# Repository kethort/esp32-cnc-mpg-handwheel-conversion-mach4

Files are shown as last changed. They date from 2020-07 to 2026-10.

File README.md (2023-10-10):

# Mach4 Wireless (Wifi) MPG Handwheel Using ESP32 and Modbus TCP library

<p align="center">
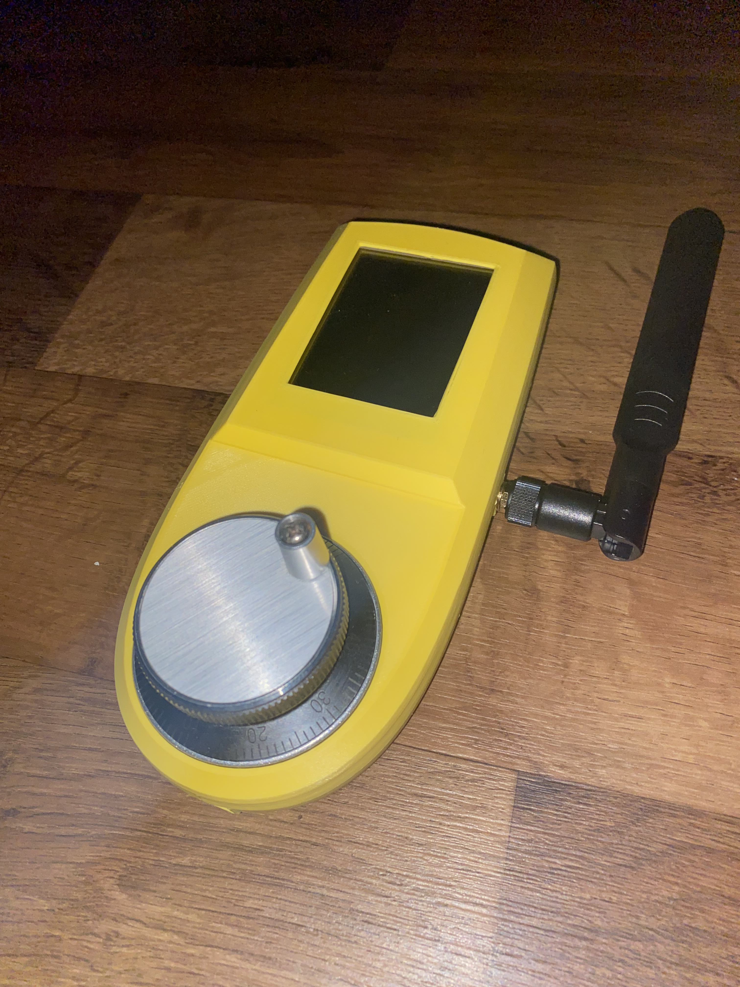
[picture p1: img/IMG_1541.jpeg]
  
</p>

<p align="center">
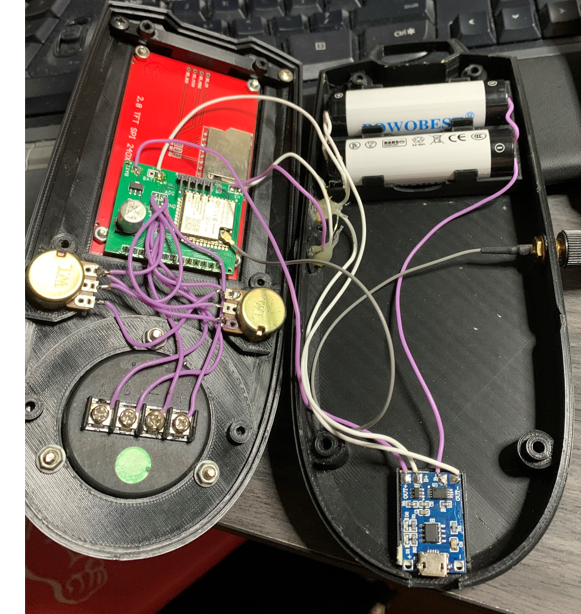
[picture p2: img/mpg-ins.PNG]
  
</p>

## Demonstration & Assembly
https://www.youtube.com/watch?v=sGhttK0reT0&t=2s <br>
https://www.youtube.com/watch?v=5fpQ3xS1Tu8&t=2s

## ESP32 Firmware and Network Setup
1. Download NodeMCU-PyFlasher.exe program from here: https://github.com/marcelstoer/nodemcu-pyflasher/releases/tag/v5.0.0
2. Connect a USB to FTDI or CP2102 to FTL programmer to the ESP32 PCB at the programmer port. 
3. Select the COM port of the programmer in the NodeMCU program.
4. Select the Mach4MPGModbus-ILI9341-Display.ino.bin file from the fw-build folder and press the Flash NodeMCU button to flash the firmware to the ESP32.
5. Reboot the ESP32.

<p align="center">
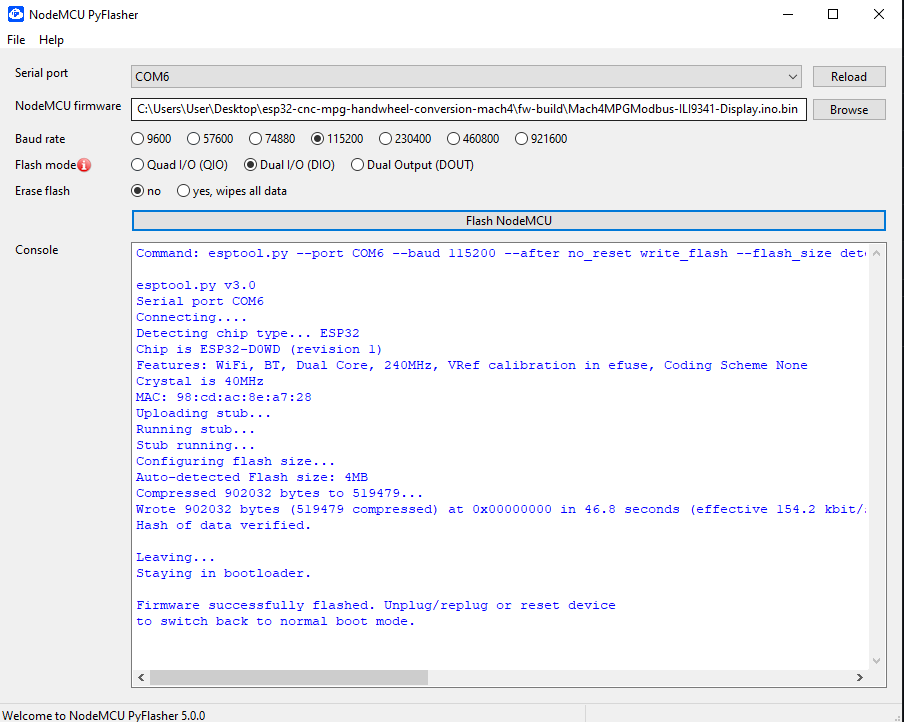
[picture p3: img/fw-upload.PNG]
  
</p>

6. The ESP32 device should show up in the list of network access points. 

<p align="center">
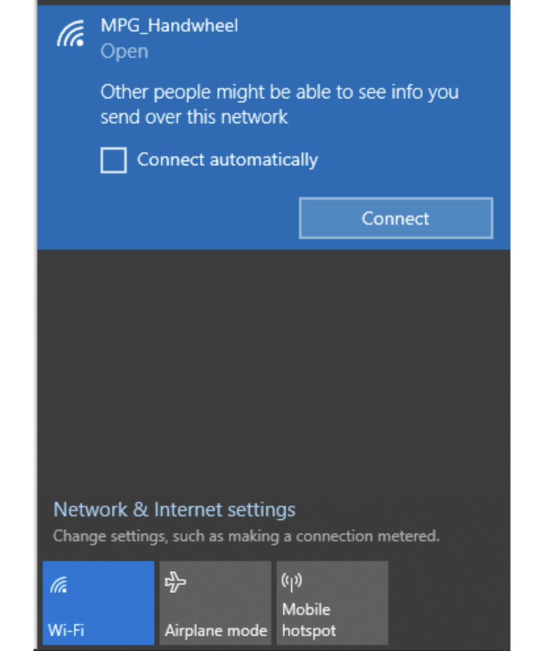
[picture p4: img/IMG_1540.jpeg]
  
</p>

7. Connect to this access point and navigate to 192.168.4.1 in a browser. 
8. Press the "Configure Wifi" button.

<p align="center">
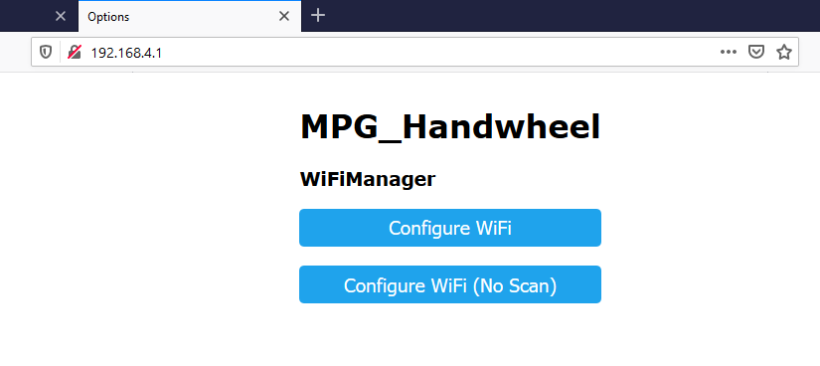
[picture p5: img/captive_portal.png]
  
</p>

9. Find your network access point and connect to it by providing your network credentials.

<p align="center">
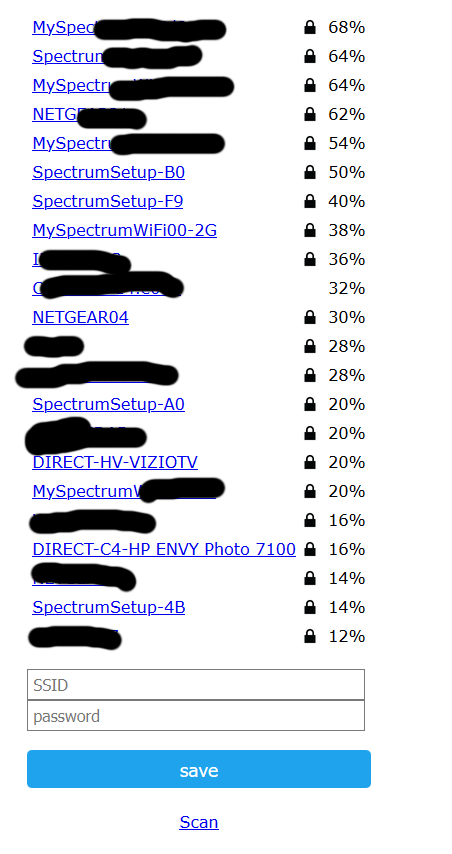
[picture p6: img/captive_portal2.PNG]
  
</p>

## Mach4 Software Setup
1. Find the local IP address of the ESP32 (espressif). 

<p align="center">
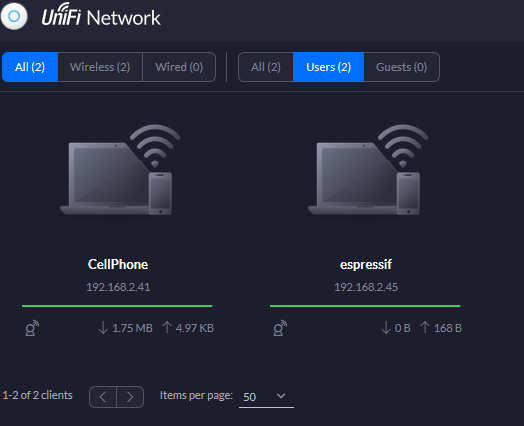
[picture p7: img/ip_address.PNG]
  
</p>

2. Launch the MPGInstaller.exe from the dist folder of the repo.
3. Select the Mach4 profile you want to update, enter the IP address of the ESP32 and press install. (if the ESP32 device is already connected to the network, and in the ARP table, the IP address should auto-populate)

<p align="center">
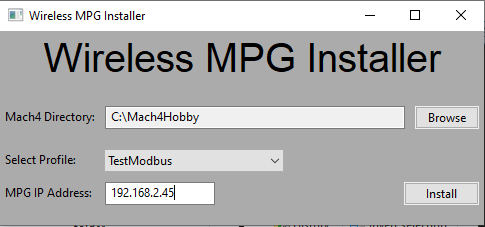
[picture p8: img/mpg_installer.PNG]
  
</p>

4. Turn on the ESP32 MPG, open Mach4 and navigate to Diagnostic->Modbus in the File Menu.
5. To connect or reconnect to the modbus device, press the stop button in the diagnostic window and then the play button. <i>(Alternatively use the Wizard instead [step 6])</i>

<p align="center">
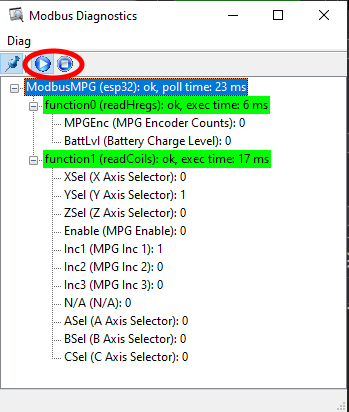
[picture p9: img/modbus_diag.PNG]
  
</p>

6. The wizard can be accessed by opening the Wizard launcher in the Mach4 file menu. (Wizard->Select Wizard->MPGWiz)
   
<p align="center">
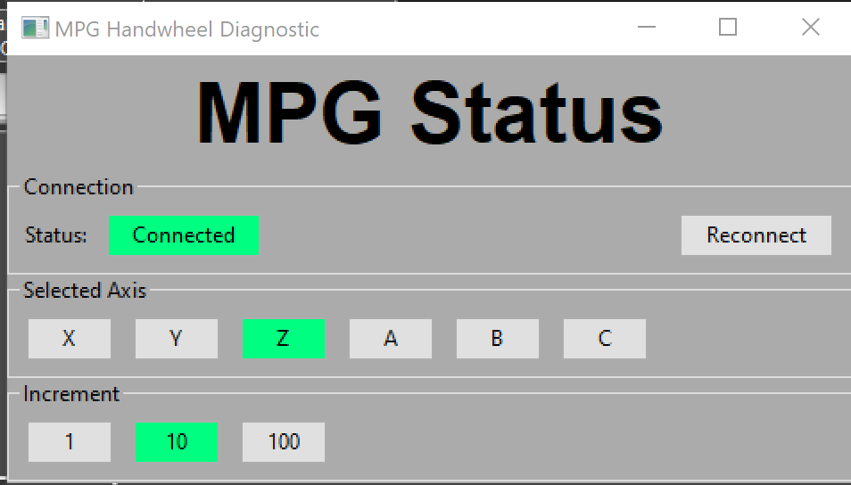
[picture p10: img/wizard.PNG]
  
</p>   

## Installer Build from Source
If you want to make changes to MPGInstaller.py and rebuild exe file:

1. Install Python
2. In elevated command line window from root directory of repo: ```pip install -r requirements.txt```
4. In command line window from root directory of repo: ```python setup.py py2exe```

The updated .exe file will be created in the dist/ folder. 

## PCB Gerber File & 3d print files for Display included
Original 3d print: https://www.thingiverse.com/thing:4539827

<p align="center">
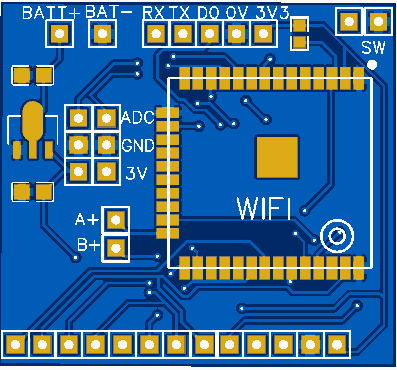
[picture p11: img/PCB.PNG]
  
</p>

<p align="center">
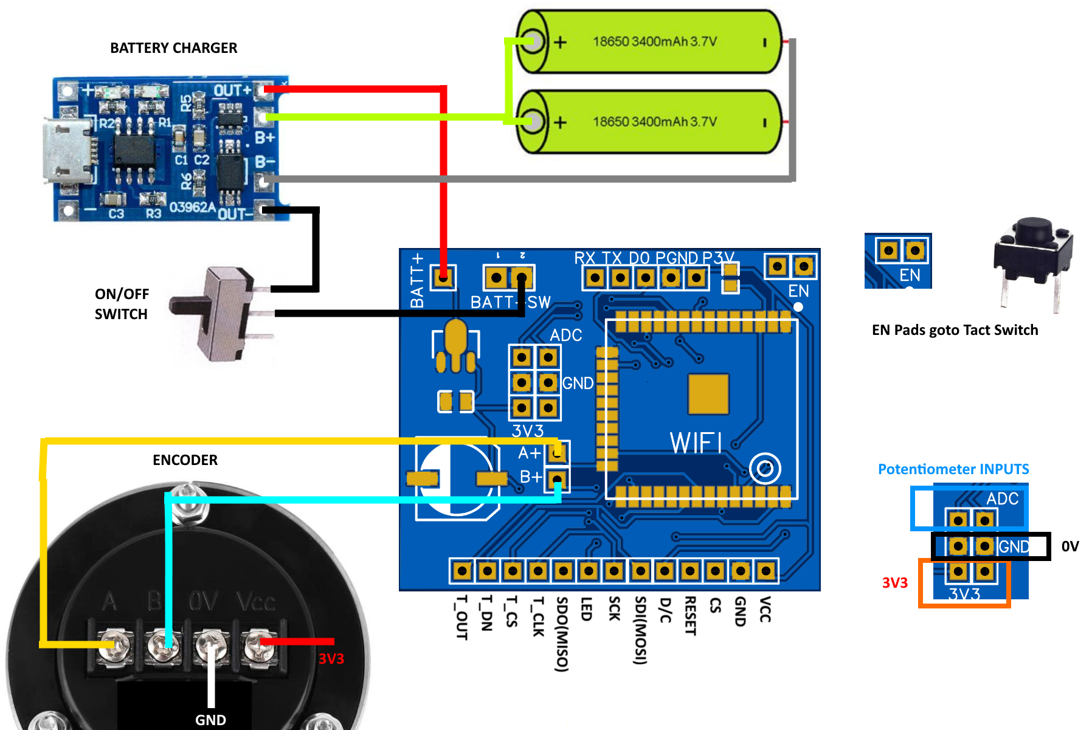
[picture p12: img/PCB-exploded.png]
  
</p>

<p align="center">
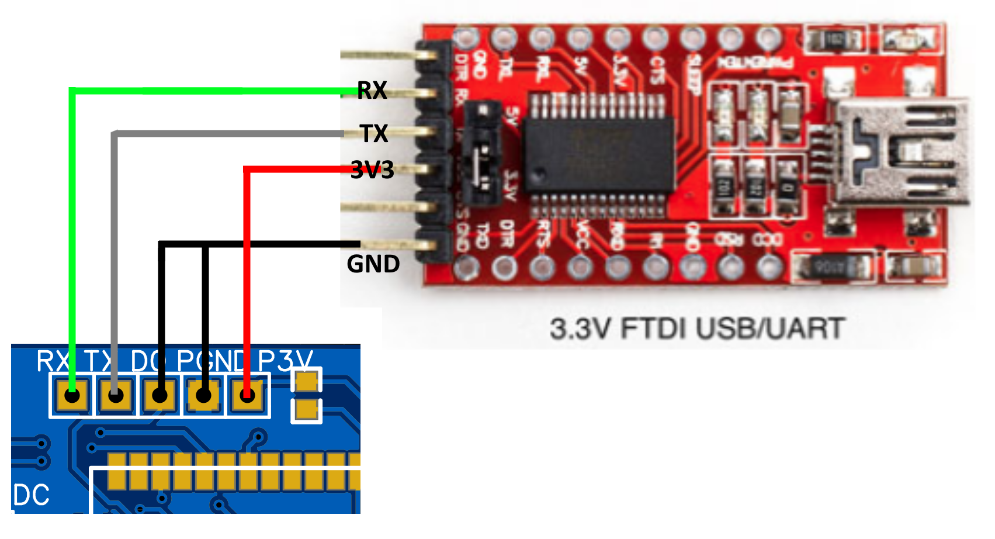
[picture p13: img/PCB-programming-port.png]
  
</p>

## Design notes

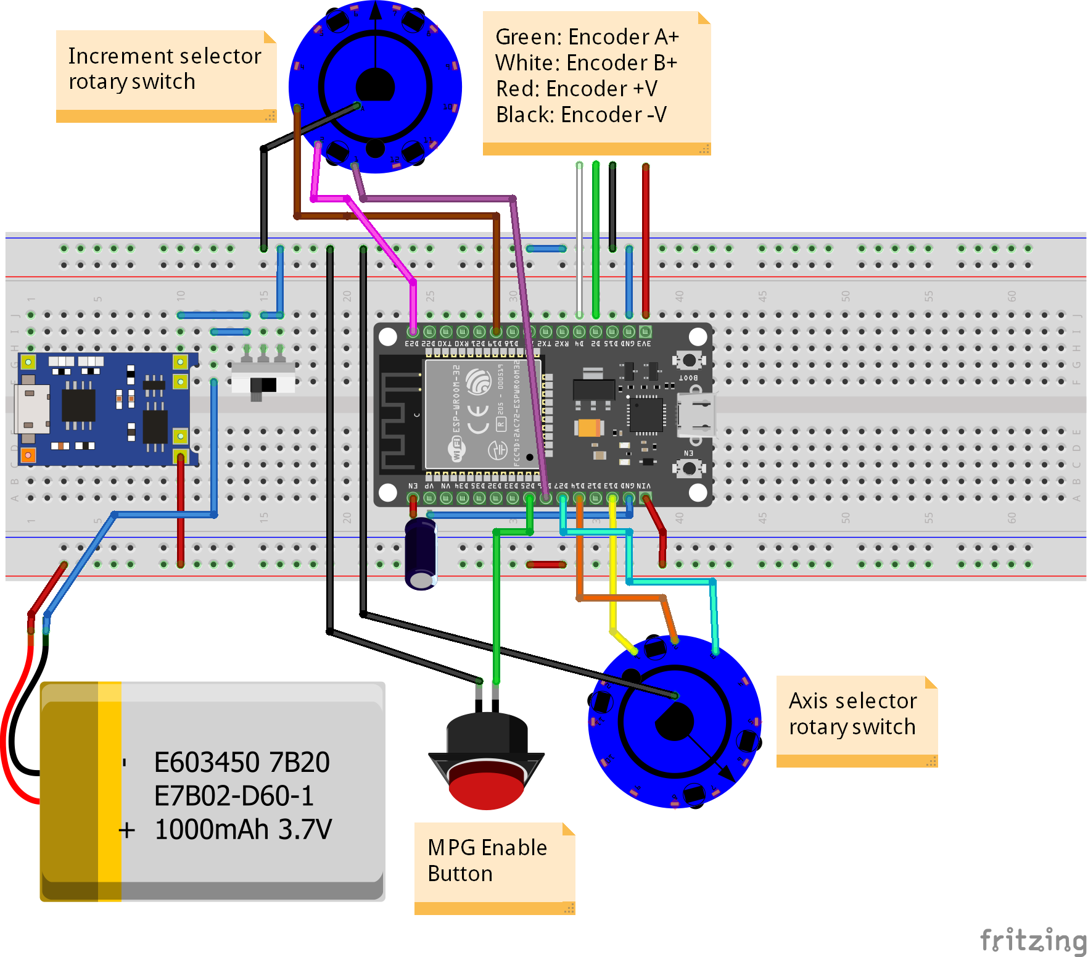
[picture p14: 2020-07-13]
img/WirelessMPG_bb.png

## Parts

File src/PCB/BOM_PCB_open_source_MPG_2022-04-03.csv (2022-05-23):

ID | Name | Designator | Footprint | Quantity | Manufacturer Part | Manufacturer | Supplier | Supplier Part | Price
1 | 1uF | C2 | C0805 | 1 | EMK212B7105KG-T | TAIYO YUDEN | LCSC | C87154 | 0.022
2 | 2.2uF | C4 | C0805 | 1 | CL21A225KOFNNNE | SAMSUNG | LCSC | C1731 | 0.022
3 | BATT- | BAT- | HDR-M-2.54_1X1 | 1 |  |  | LCSC | C81276 | 0.007
4 | BATT+ | BATT+ | HDR-M-2.54_1X1 | 1 |  |  | LCSC | C81276 | 0.007
5 | SWTCH | SWTCH | HDR-M-2.54_1X1 | 1 |  |  | LCSC | C81276 | 0.007
6 | 3V3 | 3V3,3V,J26,J10 | HDR-M-2.54_1X1 | 4 |  |  | LCSC | C81276 | 0.007
7 | D0 | D0 | HDR-M-2.54_1X1 | 1 |  |  | LCSC | C81276 | 0.007
8 | RX | RX | HDR-M-2.54_1X1 | 1 |  |  | LCSC | C81276 | 0.007
9 | TX | TX | HDR-M-2.54_1X1 | 1 |  |  | LCSC | C81276 | 0.007
10 | D25 | ADC | HDR-M-2.54_1X1 | 1 |  |  | LCSC | C81276 | 0.007
11 | D32 | SW | HDR-M-2.54_1X1 | 1 |  |  | LCSC | C81276 | 0.007
12 | GND | 0V,GND,J24,J9 | HDR-M-2.54_1X1 | 4 |  |  | LCSC | C81276 | 0.007
13 | D2 | A+ | HDR-M-2.54_1X1 | 1 |  |  | LCSC | C81276 | 0.007
14 | D4 | B+ | HDR-M-2.54_1X1 | 1 |  |  | LCSC | C81276 | 0.007
15 | HT7833 | U2 | SOT-89_L4.5-W2.5-P1.50-LS4.2-BR | 1 | HT7833 | HOLTEK | LCSC | C50936 | 0.564
16 | ESP32-WROOM-32U | U1 | WIFIM-SMD_38P-L19.2-W18.0-P1.27 | 1 | ESP32-WROOM-32U | Espressif Systems | LCSC | C328062 | 3.244
17 | D27 | J14 | HDR-M-2.54_1X1 | 1 |  |  | LCSC | C81276 | 0.007
18 | D26 | J23 | HDR-M-2.54_1X1 | 1 |  |  | LCSC | C81276 | 0.007
19 | 10K | R1 | R0603 | 1 | SDNT1608X103F3450FTF | Sunlord | LCSC | C95953 | 0.024
20 | D23 | J13,J5 | HDR-M-2.54_1X1 | 2 |  |  | LCSC | C81276 | 0.007
21 | EN | J2 | HDR-M-2.54_1X1 | 1 |  |  | LCSC | C81276 | 0.007
22 | D13 | J3 | HDR-M-2.54_1X1 | 1 |  |  | LCSC | C81276 | 0.007
23 | D15 | J4 | HDR-M-2.54_1X1 | 1 |  |  | LCSC | C81276 | 0.007
24 | D21 | J6 | HDR-M-2.54_1X1 | 1 |  |  | LCSC | C81276 | 0.007
25 | D19 | J7 | HDR-M-2.54_1X1 | 1 |  |  | LCSC | C81276 | 0.007
26 | D18 | J8,J12 | HDR-M-2.54_1X1 | 2 |  |  | LCSC | C81276 | 0.007
27 | NC | J11 | HDR-M-2.54_1X1 | 1 |  |  | LCSC | C81276 | 0.007

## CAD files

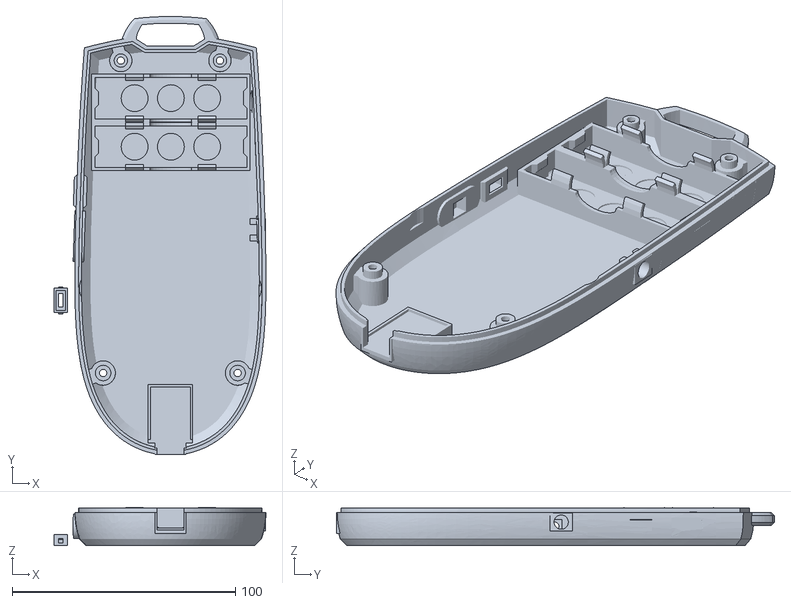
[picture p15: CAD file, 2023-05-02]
src/3d Print Files/mpg-bottom.stl
95.0 x 196.2 x 17.2

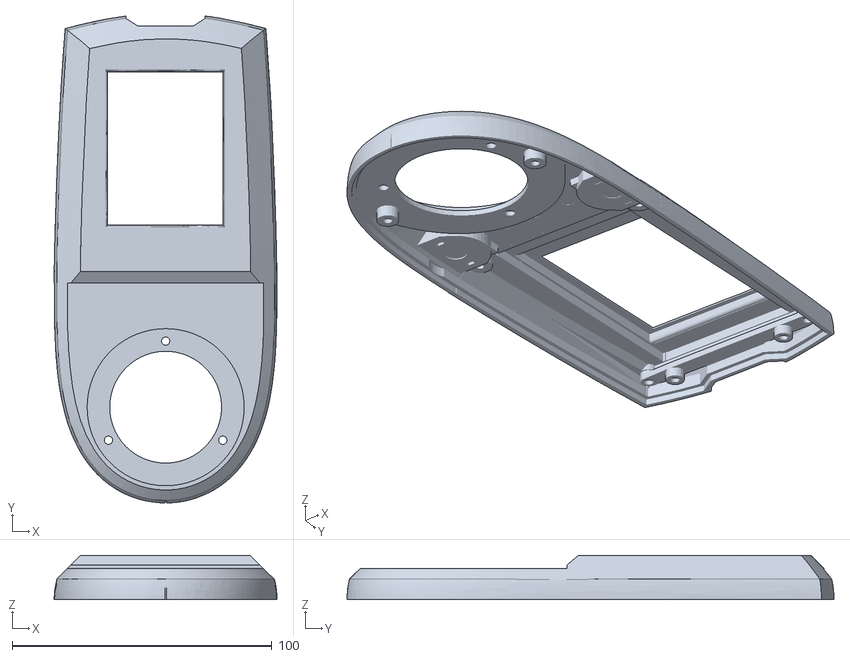
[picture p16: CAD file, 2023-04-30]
src/3d Print Files/mpg-top-no-knobs.stl
85.8 x 187.4 x 16.9

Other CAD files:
src/3d Print Files/mpg-top.stl

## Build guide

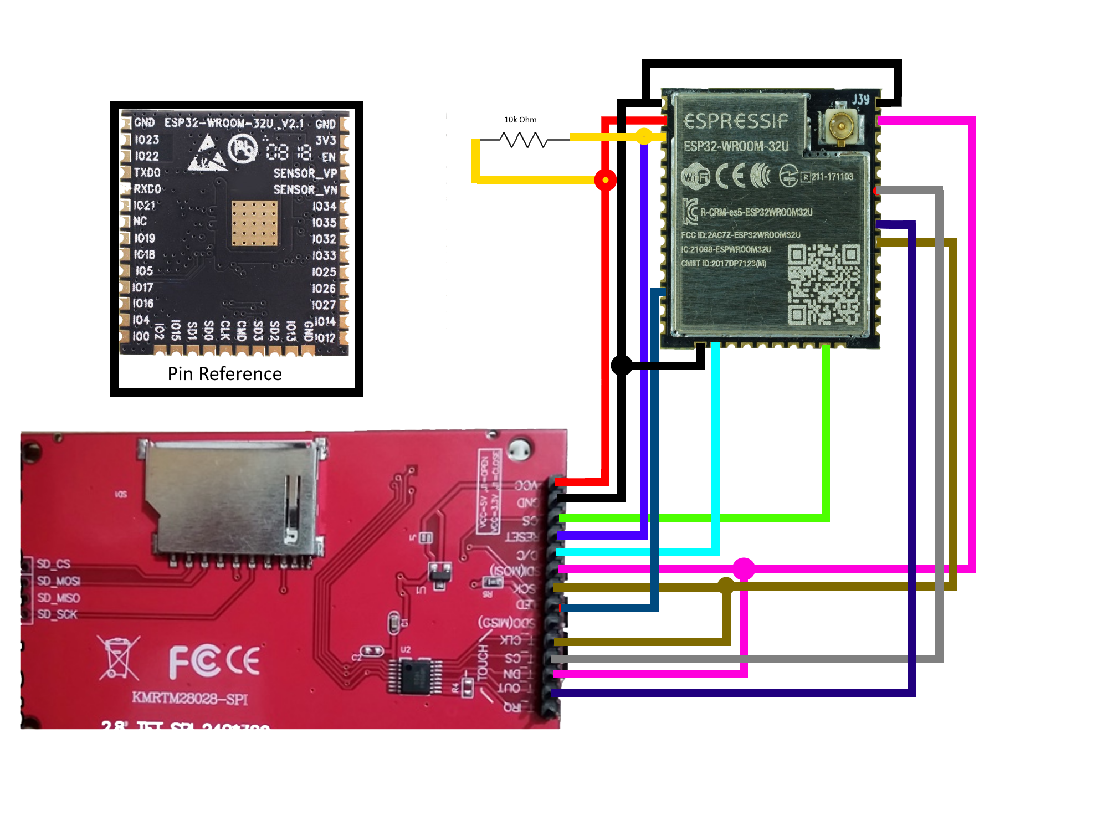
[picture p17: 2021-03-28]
img/esp32-ili9341-wiring.png

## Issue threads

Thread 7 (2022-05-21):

can't find Network WIFI After burn firmware

abdulasis12, 2022-05-21:
Hi, I'm sis .
I try  many times for burn firmware. After done, I leave all wire and connect 3.7VDC from battery 18650 to PCB , I try check Voltage at capacitor it's recieved about 3.3V (corect) . Then I Turn on WIFI on mobile for search Network but can't found it . how to fix this problem ?

kethort, 2022-05-21:
hello sis,

The calibration of the ILI9341 screen takes place in the code before the WiFi setup. The program will block until the calibration is complete. So, if you don't have a display connected to the PCB, then you can comment out the touch screen calibration in the code so that it goes directly to the WiFi setup.

`void setup(void)
{
  pinMode(SCRLED, OUTPUT);
  digitalWrite(SCRLED, HIGH);

  tft.init();

  // Set the rotation before we calibrate
  tft.setRotation(0);

  // call screen calibration
  //touch_calibrate();                // comment out this line

  drawWifiUpdateScreen();
  WiFiManager wifiManager;
  wifiManager.autoConnect("MPG_Handwheel");
`

abdulasis12, 2022-05-22:
Hi kethort,
Hi Open  file Mach4MPGModbus-ILI9341-Display.ino via Arduino IDE.
Then I comment from you told on   >>    **//touch_calibrate();**
I try compile
it's show Error PNCT  in ESP32Encoder.cpp , Can't upload firmware.
Can you help me ?

`C:\Program Files (x86)\Arduino\libraries\ESP32Encoder-master\src\ESP32Encoder.cpp: In function 'void pcnt_example_intr_handler(void*)':
C:\Program Files (x86)\Arduino\libraries\ESP32Encoder-master\src\ESP32Encoder.cpp:41:25: error: 'PCNT' was not declared in this scope
  uint32_t intr_status = PCNT.int_st.val;
                         ^~~~
C:\Program Files (x86)\Arduino\libraries\ESP32Encoder-master\src\ESP32Encoder.cpp:41:25: note: suggested alternative: 'OCT'
  uint32_t intr_status = PCNT.int_st.val;
                         ^~~~
                         OCT
`

kethort, 2022-05-23:
hello,

try updating the ESP32Encoder library as suggested in the last comment here:
https://github.com/espressif/arduino-esp32/issues/5823

I will update the repo with the updated library.

abdulasis12, 2022-05-23:
Hi Kethort,
Thank you for answer, Now I'm update done.
And new error after compile   >>>>  **### TFT_eSPI.h:306:21: error: 'VSPI' was not declared in this scope**
please help me one more :)

`In file included from C:\Users\abdul\OneDrive\Arduino\CNC\Arix Machine\esp32-cnc-mpg-handwheel-conversion-mach4-master\esp32-cnc-mpg-handwheel-conversion-mach4-master\Arduino\Mach4MPGModbus-ILI9341-Display\Mach4MPGModbus-ILI9341-Display.ino:18:
C:\Program Files (x86)\Arduino\libraries\TFT_eSPI/TFT_eSPI.h:306:21: error: 'VSPI' was not declared in this scope
     uint8_t  port = VSPI;
                     ^~~~
C:\Program Files (x86)\Arduino\libraries\TFT_eSPI/TFT_eSPI.h:306:21: note: suggested alternative: 'SPI'
     uint8_t  port = VSPI;
                     ^~~~
                     SPI
`

abdulasis12, 2022-05-23:
Hi Kethort
I have update.
After update esp32Encoder I can compile , I try upload with comment out line  //touch_calibrate();
Now, ESP32 can show Wifi  MPG_Hanwheel    :)
About next 3-4 days  I will recieved new TFT I will try connect new TFT with PCB and test again.
Thank you very much bro :)

kethort, 2022-05-23:
this project was designed to use an ILI9341 display attached to the PCB. If you don't have that configuration, I can't help you with compilation problems. I keep the firmware bin's updated on this repo in regards to the configuration that is specific to the design of this project. I've compiled this on multiple separate computers with no issues. I don't know what environment you are using to compile the code so I cannot help you.

My guess, from google searching your issues, is that you aren't compiling the firmware with the correct board selected. It should be "ESP32 Dev Module" in the board selection in Arduino. But, I have no idea how you are compiling the firmware so, I can't help you.

If you have the ILI9341 display connected to the PCB then you do not have to edit the source code and you can easily flash the bin files I provided in the repo using an FTDI programmer.

abdulasis12, 2022-05-23:
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

Thank you ,
Now I have ILI9341 and PCB from your and first day I ask about this issue all connected ESP32 + PCB + TFT + and resistor, capacitor regulator.
I can upload done (with your .bin file) but not show anything on TFT after re-power I think maybe TFT crash  now i order new TFT waiting 3-4 days i will try again.
Thank you bro  :)

kethort, 2022-05-24:
hello,

It looks like you are using the older version of the PCB design. One thing to note about that is, the first LDO voltage regulator I chose (ht7333a) can only provide 250mA of power and the screen would sometimes not turn on. I upgraded it to use an ht7833 LDO regulator instead which provides 500mA of power which is recommended by ESP32 datasheet.

Also note, there is code in the firmware to timeout the screen if no activity for 30 seconds. The screen LED is connected to an output pin on the ESP32. To wake it up either touch the screen or press the enable button, which is not wired up in the picture you provided.

abdulasis12, 2022-05-24:
If I use old version PCB will a problem or not ?  If new version better I will new order and wait 1 month for recieve it.
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

abdulasis12, 2022-05-24:
NEW PCB  with 78L33 (can't find HT7833 local must china order) use old PCB
I will update tomorow for result
Thank you.
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

kethort, 2022-05-31:
yeah the old PCB will work. i mean...it's literally in the youtube video link. everything is in the repo.  HT7833 is on ebay... easy.  I hope you know that Google exists. I can't help you every step of the way in your life.

Closed 2022-05-23.

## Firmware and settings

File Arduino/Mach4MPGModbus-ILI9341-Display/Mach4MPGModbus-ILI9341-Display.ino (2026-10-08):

#include <WiFi.h>
#include <DNSServer.h>
#include <WebServer.h>
#include <WiFiManager.h> 
#include <ModbusIP_ESP8266.h>
#include <ESP32Encoder.h>
#include <ESPmDNS.h>
#include <WiFiUdp.h>
#include <ArduinoOTA.h>

ModbusIP mb;
int regs[] = {1,  2,  3,  9,  10, 11, 4,  5,  6,  7, 12, 13, 14}; 

ESP32Encoder encoder;

#include "FS.h"
#include <SPI.h>
#include <TFT_eSPI.h> 
#include <TFT_eSPI_TouchUI.h>

//#define DEBUG // enables Serial

// This is the file name used to store the touch coordinate
// calibration data. Change the name to start a new calibration.
#define CALIBRATION_FILE "/TouchCalData2"

// Set REPEAT_CAL to true instead of false to run calibration
// again, otherwise it will only be done once.
// Repeat calibration if you change the screen rotation.
#define REPEAT_CAL false

TFT_eSPI tft = TFT_eSPI();       
TFT_eSPI_TouchUI slider[3];

#define SLIDER_MIN 0
#define SLIDER_MAX 100
#define SLIDER_BTN_W 20
#define SLIDER_BAR_L 180

#define MIDBUTTON_W 72
#define MIDBUTTON_H 50

#define NAVBUTTON_H 40

#define SMALLBTN_W (MIDBUTTON_W / 2)
#define SMALLBTN_H  MIDBUTTON_H

#define IP_ADDR_X 120
#define IP_ADDR_Y 20

#define CONTROLBUTTON_X 5
#define CONTROLBUTTON_Y 275

#define MPGBUTTON_X 85
#define MPGBUTTON_Y 275

#define SPEEDBUTTON_X 164
#define SPEEDBUTTON_Y 275

#define BACKBUTTON_X 85
#define BACKBUTTON_Y 275

#define MPGEN 32
#define SCRLED 27
#define ADC0 25
#define ADC1 26

byte pageNum;
float lastDRODecimal[6];
uint32_t lastUpdatePercent;

#define SCR_TMOUT 30000
uint32_t screenTime = 0; 
bool screenActive = true;

void setup(void)
{
  pinMode(SCRLED, OUTPUT);
  digitalWrite(SCRLED, HIGH);

  tft.init();

  // Set the rotation before we calibrate
  tft.setRotation(0);

  // call screen calibration
  touch_calibrate();

  drawWifiUpdateScreen();
  WiFiManager wifiManager;
  wifiManager.autoConnect("MPG_Handwheel");

#ifdef DEBUG
  Serial.begin(115200);
  Serial.println("WiFi connected");  
  Serial.println("IP address: ");
  Serial.println(WiFi.localIP());
#endif
  
  setupOTA("MPG_Handwheel");
  mb.server();

  pinMode(MPGEN, INPUT_PULLUP);

  // button state coils
  for(int i = 0; i < sizeof(regs)/sizeof(regs[0]); i++) {
    mb.addCoil(regs[i]); 
  }

  encoder.attachFullQuad(4, 2);
  encoder.clearCount();
  mb.addHreg(55); // encoder counts modbus register

  // DRO registers (99 - 110)
  // Slider Mach4 write registers (111 - 113)
  // Mach4 status register (114)
  for(int i = 99; i < 115; i++)
    mb.addHreg(i);

  // Slider Mach4 read registers (56 - 58)
  mb.addHreg(56);
  mb.addHreg(57);
  mb.addHreg(58);

  // Control register 59
  mb.addHreg(59);
  mb.Hreg(59, 555);
  
  drawDROPage();

  slider[0].initSliderH(&tft, SLIDER_MIN, SLIDER_MAX, 50, 80, SLIDER_BTN_W, SLIDER_BAR_L, TFT_WHITE, TFT_DARKGREY, TFT_BLACK, 1, 0);
  screenTime = millis();
}

void loop() {
  ArduinoOTA.handle();
  mb.task();
  mb.Coil(regs[6], !digitalRead(MPGEN));

  // forces encoder count rollover to zero instead of int16_t max/min
  if((int16_t)encoder.getCount() > 32760 ||(int16_t)encoder.getCount() < -32760){
    encoder.clearCount();
    mb.Hreg(55, 0);
  }

  // only get encoder counts when the MPG enable button is pressed
  if(!digitalRead(MPGEN)) {
    encoder.resumeCount();
    mb.Hreg(55, (int16_t)encoder.getCount());
    screenTime = millis();
    digitalWrite(SCRLED, HIGH);
  } else {
    encoder.pauseCount();
  }

  // turn off the screen if no touch for 30 seconds
  if (millis() - screenTime >= SCR_TMOUT) {
    screenActive = false;
    digitalWrite(SCRLED, LOW);
  }
  
  switch(pageNum) {
    case 1:
      updateDROs();
      getTouchDROPage();
      break;
    case 2:
      getTouchControlPage();
      break;
    case 3:
      getTouchMPGPage();
      break;
    case 4:
      getTouchSliderPage();
      break;
    case 5:
      getTouchAxisControlPage();
      break;
  }
}

bool boundingBoxPressed(uint16_t xLoc, uint16_t yLoc, int16_t xMin, int16_t xMax, int16_t yMin, int16_t yMax) {
  if ((xLoc > xMin) && (xLoc <= xMax)) {
    if ((yLoc > yMin) && (yLoc <= yMax)) {
      return true;    
    }
  }
  return false;
}

void drawButtonOnScreen(const char *label, uint16_t xLoc, uint16_t yLoc, uint16_t xWidth, uint16_t yHeight) {
  tft.fillRect(xLoc, yLoc, xWidth, yHeight, TFT_DARKGREY);
  tft.setTextColor(TFT_BLACK);
  tft.setTextSize(2);
  tft.setTextDatum(MC_DATUM);
  tft.drawString(label, xLoc + (xWidth / 2), yLoc + (yHeight / 2));
}

void highlightButton(void (*drawButtonsFunc)(void), int32_t x, int32_t y, int32_t w, int32_t h, const char *label) {
  drawButtonsFunc();
  tft.fillRect(x, y, w, h, TFT_GREEN);
  tft.setTextColor(TFT_BLACK);
  tft.setTextSize(2);
  tft.setTextDatum(MC_DATUM);
  tft.drawString(label, x + (w / 2), y + (h / 2));
}

void drawWifiUpdateScreen() {
  pageNum = 0;
  
  tft.fillScreen(TFT_BLACK); 
  tft.setTextColor(TFT_WHITE);
  tft.setTextSize(2);
  tft.setTextDatum(MC_DATUM);
  tft.drawString("WiFi", 125, 100);
  tft.drawString("Connecting", 125, 130); 
}

void drawOTAUpdateScreen() {
  pageNum = 0;
  
  tft.fillScreen(TFT_BLACK); 
  tft.setTextColor(TFT_WHITE);
  tft.setTextSize(2);
  tft.setTextDatum(MC_DATUM);
  tft.drawString("Updating", 125, 100);
  tft.drawString("Firmware", 125, 130); 
}

void showOTAUpdateProgress(unsigned int progress, unsigned int total) {
  char strBfr[50];
  
  tft.setTextColor(TFT_BLACK);
  tft.setTextSize(2);
  tft.setTextDatum(MC_DATUM);
  sprintf(strBfr, "%u%%", lastUpdatePercent);
  tft.drawString(strBfr, 125, 160);
  lastUpdatePercent = (progress / (total / 100));
  memset(strBfr, 0, sizeof(strBfr));

  tft.setTextColor(TFT_WHITE);
  tft.setTextSize(2);
  tft.setTextDatum(MC_DATUM);
  sprintf(strBfr, "%u%%", (progress / (total / 100)));
  tft.drawString(strBfr, 125, 160);
  memset(strBfr, 0, sizeof(strBfr));
}

void setupOTA(const char* nameprefix) {
  // Configure the hostname
  uint16_t maxlen = strlen(nameprefix) + 7;
  char *fullhostname = new char[maxlen];
  uint8_t mac[6];
  WiFi.macAddress(mac);
  snprintf(fullhostname, maxlen, "%s-%02x%02x%02x", nameprefix, mac[3], mac[4], mac[5]);
  ArduinoOTA.setHostname(fullhostname);
  delete[] fullhostname;

  ArduinoOTA.onStart([]() {
    // turn the screen on if it's off
    screenActive = true;
    digitalWrite(SCRLED, HIGH);
    drawOTAUpdateScreen();
  });
  
  ArduinoOTA.onEnd([]() {
  });
  
  ArduinoOTA.onProgress([](unsigned int progress, unsigned int total) {
    showOTAUpdateProgress(progress, total);
  });
  
  ArduinoOTA.onError([](ota_error_t error) {
  });

  ArduinoOTA.begin();
}

void recalibrateTouch() {

    // Ensure screen is awake
    screenActive = true;
    digitalWrite(SCRLED, HIGH);

    // Remove the saved calibration data.
    // touch_calibrate() will see that the file is missing
    // and run a fresh calibration.
    if (SPIFFS.exists(CALIBRATION_FILE)) {
        SPIFFS.remove(CALIBRATION_FILE);
    }

    touch_calibrate();

    // Return to the CTRL screen when calibration finishes.
    drawControlPage();

    screenTime = millis();
}

void touch_calibrate() {
  uint16_t calData[5];
  uint8_t calDataOK = 0;

  // check file system exists
  if (!SPIFFS.begin()) {
#ifdef DEBUG
    Serial.println("Formatting file system");
#endif
    SPIFFS.format();
    SPIFFS.begin();
  }

  // check if calibration file exists and size is correct
  if (SPIFFS.exists(CALIBRATION_FILE)) {
    if (REPEAT_CAL)
    {
      // Delete if we want to re-calibrate
      SPIFFS.remove(CALIBRATION_FILE);
    }
    else
    {
      File f = SPIFFS.open(CALIBRATION_FILE, "r");
      if (f) {
        if (f.readBytes((char *)calData, 14) == 14)
          calDataOK = 1;
        f.close();
      }
    }
  }

  if (calDataOK && !REPEAT_CAL) {
    // calibration data valid
    tft.setTouch(calData);
  } else {
    // data not valid so recalibrate
    tft.fillScreen(TFT_BLACK);
    tft.setCursor(20, 0);
    tft.setTextFont(2);
    tft.setTextSize(1);
    tft.setTextColor(TFT_WHITE, TFT_BLACK);

    tft.println("Touch corners as indicated");

    tft.setTextFont(1);
    tft.println();

    if (REPEAT_CAL) {
      tft.setTextColor(TFT_RED, TFT_BLACK);
      tft.println("Set REPEAT_CAL to false to stop this running again!");
    }

    tft.calibrateTouch(calData, TFT_MAGENTA, TFT_BLACK, 15);

    tft.setTextColor(TFT_GREEN, TFT_BLACK);
    tft.println("Calibration complete!");

    // store data
    File f = SPIFFS.open(CALIBRATION_FILE, "w");
    if (f) {
      f.write((const unsigned char *)calData, 14);
      f.close();
    }
  }
}

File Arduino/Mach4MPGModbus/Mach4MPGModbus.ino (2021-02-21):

#include <WiFi.h>
#include <DNSServer.h>
#include <WebServer.h>
#include <WiFiManager.h> 
#include <ModbusIP_ESP8266.h>
#include <ESP32Encoder.h>

#define ADC_DIV 40
const int numReadings = 10;
int readings[numReadings];      // the readings from the analog input
int readIndex = 0;              // the index of the current reading
int total = 0;                  // the running total
int average = 0;                // the average
int adc;
#endif

//#define STATIC_IP

ModbusIP mb;
int regs[] = {1,  2,  3,  9,  10, 11, 4,  5,  6,  7}; 
int pins[] = {13, 14, 27, 32, 35, 34, 25, 15, 21, 22};

byte currentPin;

ESP32Encoder encoder;

void setup() {
  Serial.begin(115200);

  for (int thisReading = 0; thisReading < numReadings; thisReading++) {
    readings[thisReading] = 0;
  }
  
  WiFiManager wifiManager;

#ifdef STATIC_IP
  IPAddress _ip = IPAddress(192, 168, 1, 222);
  IPAddress _gw = IPAddress(192, 168, 1, 1);
  IPAddress _sn = IPAddress(255, 255, 255, 0);
  
  wifiManager.setSTAStaticIPConfig(_ip, _gw, _sn);
#endif
  
  wifiManager.autoConnect("MPG_Handwheel");

  Serial.println("WiFi connected");  
  Serial.println("IP address: ");
  Serial.println(WiFi.localIP());
        
  mb.server();

  for(int i = 0; i < sizeof(regs)/sizeof(regs[0]); i++) {
    pinMode(pins[i], INPUT_PULLUP);
    mb.addCoil(regs[i]); 
  } 

  // inputs 2 and 4 are A+ and B+ on the MPG Handwheel
  encoder.attachFullQuad(2, 4);
  encoder.clearCount();
  mb.addHreg(55); // encoder counts modbus register
  mb.addHreg(56); // ADC register
}

int smoothADCReading() {
  // subtract the last reading:
  total = total - readings[readIndex];
  // read from the sensor:
  readings[readIndex] = analogRead(33);
  // add the reading to the total:
  total = total + readings[readIndex];
  // advance to the next position in the array:
  readIndex++;

  // if we're at the end of the array...
  if (readIndex >= numReadings) {
    readIndex = 0;
  }

  // return the average:
  return(total / numReadings);
}

void loop() {
  mb.task();

  average = smoothADCReading();
  
  // constrain the adc reading to values 0 - 100
  adc = (average / ADC_DIV) - 2; 
  
  if (!(adc >= 0 && adc <= 100))
    adc = 0;
    
  mb.Hreg(56, adc);

  for(int i = 0; i < sizeof(regs)/sizeof(regs[0]); i++)
  {
    // clear the encoder count if the axis input changes
    if (!digitalRead(pins[i]) && i < 6 && currentPin != pins[i]) {
        currentPin = pins[i];
        encoder.clearCount();
        mb.Hreg(55, 0);
    }
    
    mb.Coil(regs[i], !digitalRead(pins[i]));
  }

  // forces encoder count rollover to zero instead of int16_t max/min
  if((int16_t)encoder.getCount() > 32760 ||(int16_t)encoder.getCount() < -32760){
    encoder.clearCount();
    mb.Hreg(55, 0);
  }

  // only get encoder counts when the MPG enable button is pressed
  if(!digitalRead(25)) {
    encoder.resumeCount();
    mb.Hreg(55, (int16_t)encoder.getCount());
  } else {
    encoder.pauseCount();
  }
}

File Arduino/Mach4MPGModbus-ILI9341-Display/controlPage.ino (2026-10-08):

#define ENABLEBUTTON_X 5
#define ENABLEBUTTON_Y 5

#define HOMEBUTTON_X 85
#define HOMEBUTTON_Y 5

#define STARTBUTTON_X 164
#define STARTBUTTON_Y 5

#define PAUSEBUTTON_X 5
#define PAUSEBUTTON_Y 65

#define AXESBUTTON_X 85
#define AXESBUTTON_Y 65

#define BATTBUTTON_X 164
#define BATTBUTTON_Y 65

// New touchscreen calibration button
#define CALBUTTON_X 5
#define CALBUTTON_Y 125
#define CALBUTTON_W 152
#define CALBUTTON_H MIDBUTTON_H


void drawControlPage() {

    pageNum = 2;

    tft.fillScreen(TFT_BLACK);

    drawControlButtons();

    drawButtonOnScreen(
        "Back",
        BACKBUTTON_X,
        BACKBUTTON_Y,
        MIDBUTTON_W,
        NAVBUTTON_H
    );
}


void getTouchControlPage() {

    uint16_t x, y;

    if (tft.getTouch(&x, &y)) {

        screenTime = millis();

        if (!screenActive) {

            screenActive = true;
            digitalWrite(SCRLED, HIGH);
        }

        //-------------------------------------------------
        // Touchscreen calibration
        //-------------------------------------------------

        if (boundingBoxPressed(
                x,
                y,
                CALBUTTON_X,
                CALBUTTON_X + CALBUTTON_W,
                CALBUTTON_Y,
                CALBUTTON_Y + CALBUTTON_H)) {

            // IMPORTANT:
            // Wait for the finger that pressed the CAL
            // button to be released before starting
            // calibration. Otherwise that same press may
            // be interpreted as the first calibration point.
            while (tft.getTouch(&x, &y)) {
                delay(10);
            }

            delay(200);

            recalibrateTouch();

            return;
        }

        //-------------------------------------------------
        // Back
        //-------------------------------------------------

        if (boundingBoxPressed(
                x,
                y,
                BACKBUTTON_X,
                BACKBUTTON_X + MIDBUTTON_W,
                BACKBUTTON_Y,
                BACKBUTTON_Y + MIDBUTTON_H)) {

            drawDROPage();
        }
    }
}


void drawControlButtons() {

    drawButtonOnScreen(
        "ENABLE",
        ENABLEBUTTON_X,
        ENABLEBUTTON_Y,
        MIDBUTTON_W,
        MIDBUTTON_H
    );

    drawButtonOnScreen(
        "HOME",
        HOMEBUTTON_X,
        HOMEBUTTON_Y,
        MIDBUTTON_W,
        MIDBUTTON_H
    );

    drawButtonOnScreen(
        "START",
        STARTBUTTON_X,
        STARTBUTTON_Y,
        MIDBUTTON_W,
        MIDBUTTON_H
    );

    drawButtonOnScreen(
        "PAUSE",
        PAUSEBUTTON_X,
        PAUSEBUTTON_Y,
        MIDBUTTON_W,
        MIDBUTTON_H
    );

    drawButtonOnScreen(
        "AXES",
        AXESBUTTON_X,
        AXESBUTTON_Y,
        MIDBUTTON_W,
        MIDBUTTON_H
    );

    drawButtonOnScreen(
        "BATT",
        BATTBUTTON_X,
        BATTBUTTON_Y,
        MIDBUTTON_W,
        MIDBUTTON_H
    );

    // New calibration button
    drawButtonOnScreen(
        "CAL TOUCH",
        CALBUTTON_X,
        CALBUTTON_Y,
        CALBUTTON_W,
        CALBUTTON_H
    );
}

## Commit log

2020-07-13 updated registers and pins to match current build
2020-11-20 removed debug print
2020-12-02 find ip address of device automatically
2021-01-08 removing unused comments; tested with another modbus device
2021-01-19 added ADC control knob
2021-02-21 added DRO page to Arduino sketch
2021-02-21 added exe support for installing arduino display module
2021-03-15 added 3d print stl files
    [bottom-edit.stl, top-edit.stl]
2021-03-20 added gerber files for display pcb
2021-03-20 updated 3d print files and added gerber files
    [bottom-edit.stl, btm-mpg-with-tact.stl, top-edit.stl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]
2021-03-23 adding diagrams for wiring
2021-03-28 updated wiring diagram
2021-04-05 updated stl files, fixed display timeout bugs
    [btm-mpg-with-tact.stl, mpg-bottom.stl, mpg-top.stl]
2021-04-06 bracket to hold screen in place
    [screen-bracket.stl]
2021-04-11 added pcb design files
    [BOM_PCB_open_source_MPG_2_2021-04-08.csv, PickAndPlace_PCB_open_source_MPG_2_2021-04-08.csv]
2021-04-15 edited screen size in top 3d print file
    [mpg-top.stl]
2021-04-21 testing with new pcb, updated 3d print
    [screen-bracket.stl]
2021-04-21 put DROs on main page, updated IO in sketch for PCB
2021-04-29 changed 3d print files to fit 2x 18650 batteries
    [18650-battery-holder.stl, bottom-screen-bracket.stl, mpg-bottom-18650.stl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]
2021-04-29 update to mpg bottom case
    [mpg-bottom-18650.stl]
2021-04-30 added bottom screen bracket 3d print file. rebuilt exe
2021-05-03 created exploded view of PCB and updated 3d print files
2021-05-03 added images for PCB support
    [all-parts-18650-one-print.stl, mpg-top-pots.stl]
2021-05-06 turn the screen on before calibrating it...doh!
2021-05-12 updated stl files
    [mpg-top.stl, top-screen-bracket.stl]
2021-09-16 accidentally deleted some changes a couple of gits ago
2022-02-01 new 3d prints
    [18650-battery-holder.stl, all-parts-18650-one-print.stl, bottom-screen-bracket.stl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]
2022-02-04 updated 3d prints
    [mpg-bottom.stl, mpg-top.stl]
2022-02-04 added lcd harness to mpg top print
    [mpg-top.stl]
2022-02-19 i don't want to die
2022-03-04 mpg top 3d print no knobs
2022-03-05 updated PCB design with correct regulator
    [BOM_PCB_open_source_MPG_2022-03-05.csv, BOM_PCB_open_source_MPG_2_2021-04-08.csv, PickAndPlace_PCB_open_source_MPG_2022-03-05.csv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]
2022-03-06 refined top 3d print
2022-03-09 added inc buttons for slider page
2022-03-10 adding buttons to control page
2022-03-11 added buttons on DRO page for axis control
2022-05-23 update encoder library
    [BOM_PCB_open_source_MPG_2022-04-03.csv, PickAndPlace_PCB_open_source_MPG_2022-04-03.csv]
2023-04-30 fixed top case without knobs STL
    [mpg-top-no-knobs.stl]
2023-05-02 updated mpg bottom 3d printed case
    [mpg-bottom.stl]
2023-10-10 removed delta limit in encoder count register update
2023-10-10 removed older PCB Gerber/BOM
    [BOM_PCB_open_source_MPG_2022-03-05.csv, PickAndPlace_PCB_open_source_MPG_2022-03-05.csv]
2024-09-21 re-built for python vBuilding wheel for wxPython (setup.py) ... error
